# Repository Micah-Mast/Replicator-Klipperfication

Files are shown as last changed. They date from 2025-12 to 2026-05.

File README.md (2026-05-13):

# Replicator-Klipperfication

## Abstract

The intent of this project was to revive a MakerBot Replicator+ by replacing its proprietary control system with modern, open-source electronics. The original printer, while capable in its time, had been put out of service in part due to its discontinued parts and incompatibility with modern slicers. By installing a BTT Pi, SKR Mini E3, and open-source Klipper software, the printer was brought up to current standards while retaining its original mechanical frame and gantry system. Every part of the machine, with the exception of the frame and gantry, can now be sourced from online retailers or 3d printed. Throughout the build, several unexpected issues arose, including failures in the Pi's stock 24 V buck converter and incompatibility with the first purchased touchscreen, but these were resolved with alternative hardware. The result is a fully functional, easily maintainable printer that offers improved print quality, faster workflow, and long-term serviceability using only open-source tools and components.

<p align="center">
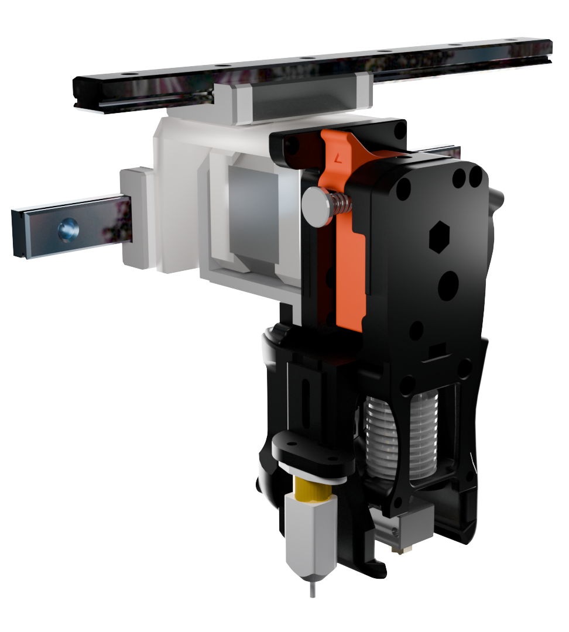
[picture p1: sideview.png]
Side view
  
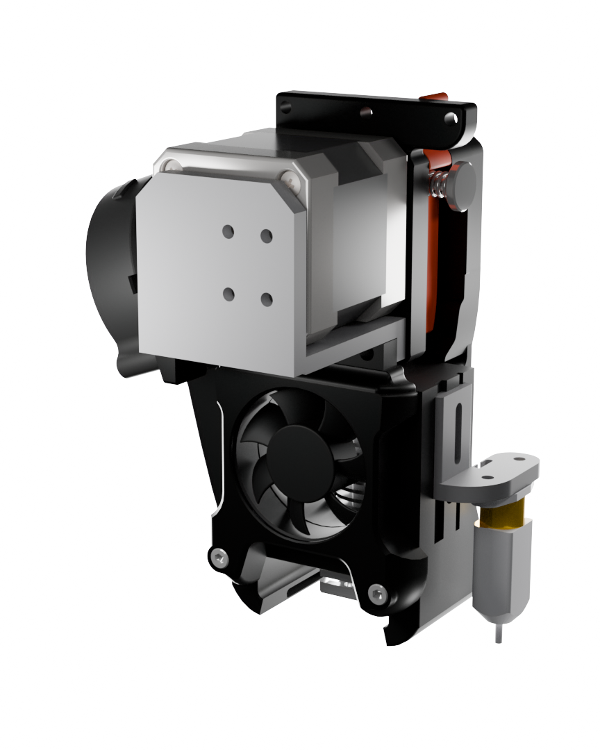
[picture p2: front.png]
Front view
  
</p>

More information can be found in the [full report](report.pdf).

## Bill Of Materials

| Component | Part | Price | Notes | Link |
|---|---|---|---|---|
| Control Board | BTT Pi V1.2 | 32 |  Stock 24v Buck converter may fail | https://a.co/d/30Qcsj7|
| Motor Controller | SKR Mini E3 V3 | 44 |  bought in combo with BTT Pi  | https://a.co/d/30Qcsj7 |
| Extruder | BMG Extruder | 6.53  | | https://www.aliexpress.us/item/3256805805447850.html |
| Heating Core | Triangle Lab CHC Pro | 5.53  | | https://www.aliexpress.us/item/3256804038017822.html |
| Heatsink + Heatbreak | V6 Heatsink | 7.58  | | https://www.aliexpress.us/item/3256802721411891.html |
| Nozzle | Came with Heatsink | | | |
| Screen | MPI3501 | 10.25 | | https://www.aliexpress.us/item/3256804172295020.html |
| Touch Panel | 3.7\" Resistive Touch Panel | 6.68  | | https://www.aliexpress.us/item/3256806894168830.html |
| BLTouch | 3DTouch | 10.87 | This is a decent BLTouch clone  | https://www.aliexpress.us/item/3256802648193836.html |
| Wires | Stepper Motor Wires | varies |  any standard stepper wires can be used | https://a.co/d/eqlczG9 |
| Power Supply | Creality 24V Power Supply | 30 | can be obtained from an Ender 3 |https://a.co/d/9iuD99J|
| Input Shaping Sensor | ADXL345 | 16 | | https://a.co/d/dzSP3lk |
| Heated Bed | Ender 3 Heated Bed | 24 | | https://a.co/d/fFlMreV |
| HDMI Adapter | Micro HDMI to HDMI Adapter | 3.49  | | https://www.aliexpress.us/item/3256803000529672.html |
| 5V Buck Converter | 24 → 5V Buck Converter | 7.49  | Overkill and only needed if onboard one fails | https://www.aliexpress.us/item/2255799834871688.html |
| Touch Screen Adapter | AR1100 Resistive Touch → USB Controller | 9.95  | | https://www.amazon.com/Noctua-NF-A4x10-24V-PWM-Applications/dp/B0CN39MCPL |

## Ideas for the Future
New Nozzle - I think the current nozzle is the main source of bad prints currently. 
Cable Management - The way the cables currently hang could very well get in the way of a print. They are also an eyesore. The wires in the back panel also need some work. Not all wires have the correct connector so they are hotglued to the controller. This has caused problems with motors vibrating loose over time.
USB hub in the UI console - Adding this would reduce the amount of wires going to the screen from 4 down to 1. The BTT-Pi can output video over USB-C so not only would the usb cables be reduced to one but the HDMI cable could be removed as well.
Input Shaping - I bought an input shaper but ran out of time to set it up fully. This would improve print quality without much effort and some of my efforts can be found in the input_shaper.cfg file.
PEI Bed - This was a result of cost, but magnetic PEI beds are not absurdly expensive for the size bed on this printer and would immediately improve the ease-of-use of the printer compared to the glass bed on there now.
Reprint Printhead in Black and Red - not a necessary upgrade but it would be nice if the actual product matched the renders.
Foodsafe Upgrade - it would be cool to turn this into a printer designated to printing food-safe filament. Really the only components that would need to be changed are the nozzle and heatbreak which need to be upgraded anyway.
Fine-Tune Slicer Settings - This is another thing that just takes time that I did not have. It just takes a lot of measuring and test prints.

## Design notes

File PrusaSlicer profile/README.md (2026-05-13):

# Using this config.ini
In PrusaSlicer under the File dropdown, choose **Import** and then **Import Config Bundle** and then navigate to the config.ini in this folder.

# Known Issue
The files for the custom bed texture and model fail to import automatically so they must be applied manually. This is not necessary for the slicer to work but it makes it look nicer.
In the **Printers** menu, click the **Set** button next to **Bed Shape** and import the files with their respective buttons.

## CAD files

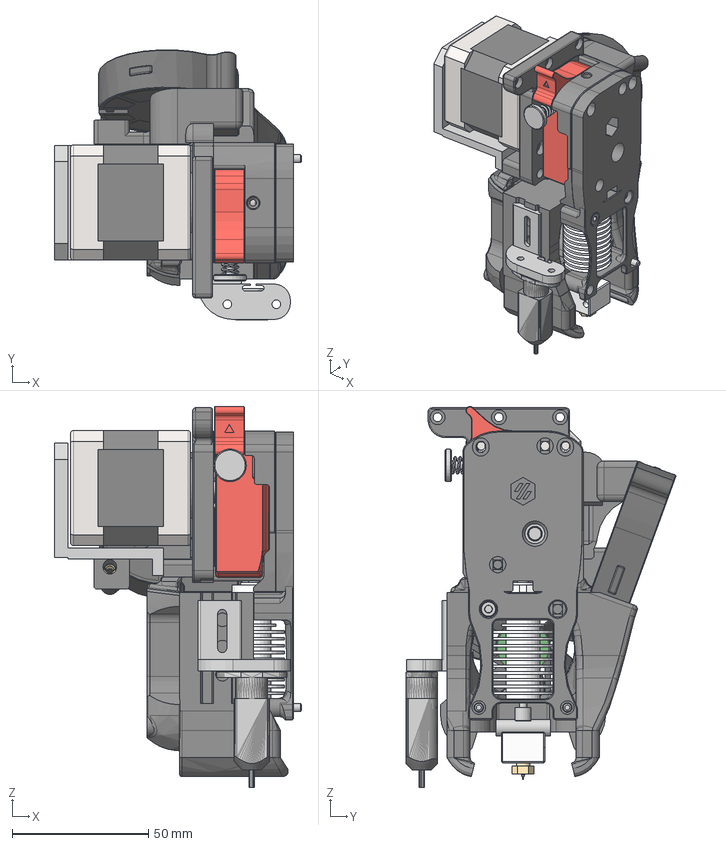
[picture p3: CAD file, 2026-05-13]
CAD/Afterburner_Assembly.step
90.8 x 99.2 x 139.9 mm
Extruder Motor Plate
shafft 3 x 20
M3x5x7 Needlebearing x 2
Direct_Drivegear_without_setscrew (1)
M3 Threaded Insert (1) x 3
M3 Thumb Screw (1)^Spring Assembly (1)_Guidler_VORON Clockwork_X Carr iage
Spring Assembly (1)-40^Spring Assembly (1)_Guidler_VORON Clockwork_X Carriage
Latch
Shaft-assembly
MR85 Ballbearing 5x8x2 x 2
Direct_Drivegear
Bowden
40x40x10 DC Fan
M3x12 SHCS (1) x 2
E3D V6 Body Rear
Heatbreak
Nozzle
Heat Block
Ceramic Cartridge Heater
Heatsink
PTFE Tube (40mm)
DragonflyBMS_Body_Front
M3x40 SHCS (3)
M3x40 SHCS (4)
M3x16 SHCS (12)
Radial_Fan_50x15
Base
Cuerpo
Tapa
pan cross head_am_B18.6.7M - M3 x 0.5 x 5 Type I Cross Recessed PHMS --5N x 4
Eje
instrument ball bearing_68_am_AFBMA 12.1.4.1 - 0050-11 - 10,SI,NC,10_ 68 x 2
socket button head cap screw_am_B18.3.4M - 3 x 0.5 x 5 SBHCS --N

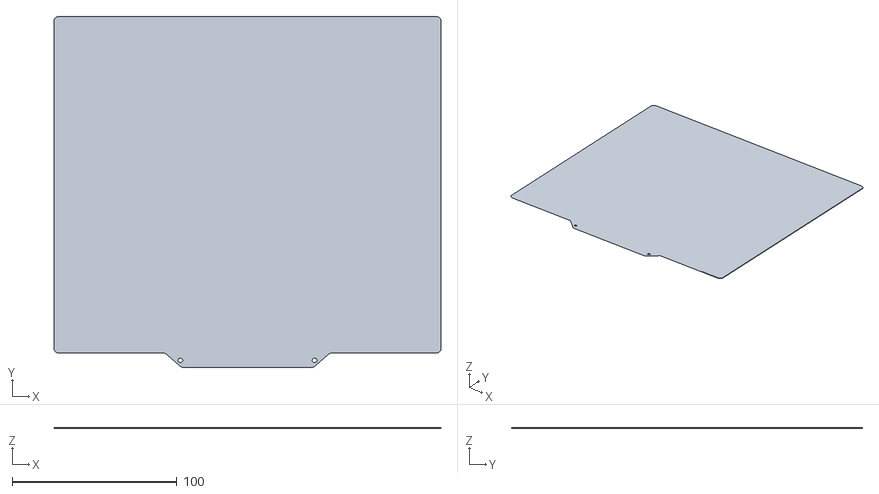
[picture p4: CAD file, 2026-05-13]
PrusaSlicer profile/replicator_bed.stl
235.0 x 213.2 x 0.5

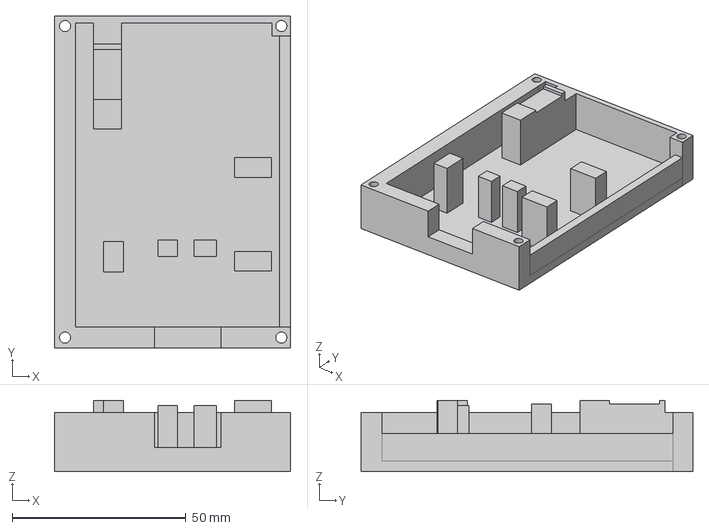
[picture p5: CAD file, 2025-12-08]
CAD/LCD_Display.step
67.9 x 95.5 x 20.5 mm

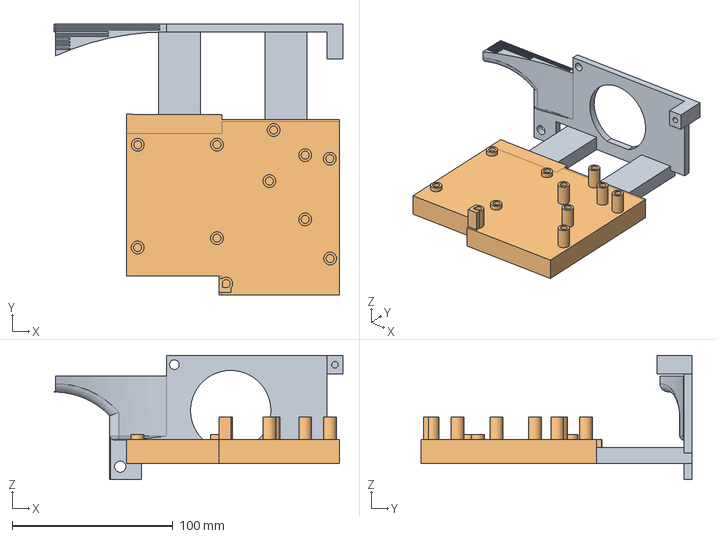
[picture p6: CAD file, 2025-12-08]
CAD/board mount.step
180.0 x 168.9 x 77.5 mm

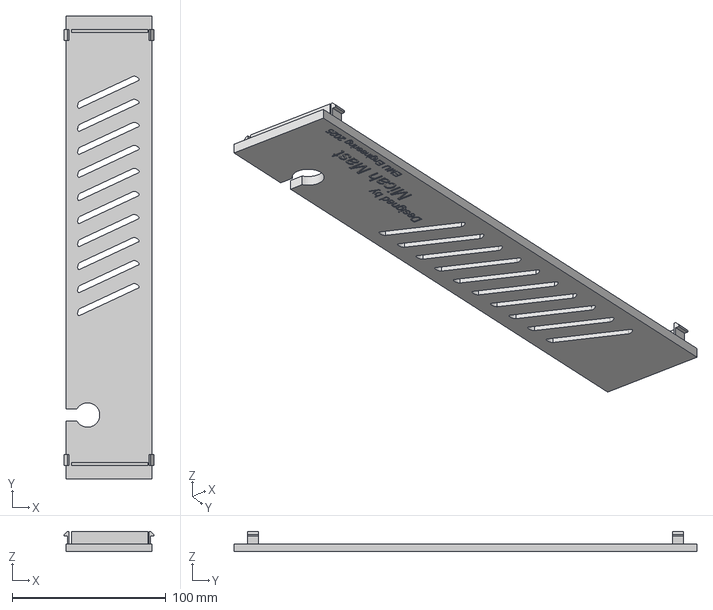
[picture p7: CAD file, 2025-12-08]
CAD/back cover.step
58.3 x 301.4 x 13.1 mm

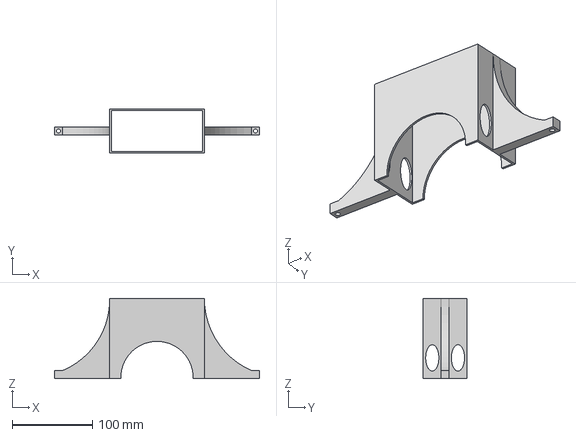
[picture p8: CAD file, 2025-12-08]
CAD/PSU mount.step
255.5 x 55.0 x 100.0 mm

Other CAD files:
CAD/LCD_Display.f3d
CAD/PSU mount.f3d
CAD/back cover.f3d

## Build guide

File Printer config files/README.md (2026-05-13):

# Using these Files
These files belong on the printer itself and can be accessed using the web GUI. The GUI can be accessed by going to replicator.local on the same network as the printer. The MAC Address can be found on a sticker on the bottom of the BTT-Pi.

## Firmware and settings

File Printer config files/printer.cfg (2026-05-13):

[include mainsail.cfg]
[include gcode_macros.cfg]
#[include input_shaper.cfg] uncomment only when calibrating input shaper and accelerometer is plugged in
#[input_shaper]
#shaper_type_x = 2hump_ei
#haper_freq_x = 68.4
#shaper_type_y = ei
#haper_freq_y = 83.8
# host MCU service is preinstalled and ready to use with:
[mcu CB1]
serial: /tmp/klipper_host_mcu

# This file contains common pin mappings for the BIGTREETECH SKR mini
# E3 v3.0. To use this config, the firmware should be compiled for the
# STM32G0B1 with a "8KiB bootloader" and USB communication/USART.

# The "make flash" command does not work on the SKR mini E3. Instead,
# after running "make", copy the generated "out/klipper.bin" file to a
# file named "firmware.bin" on an SD card and then restart the SKR
# mini E3 with that SD card.

# See docs/Config_Reference.md for a description of parameters.
[gcode_arcs]
resolution: 1.0
#   An arc will be split into segments. Each segment's length will
#   equal the resolution in mm set above. Lower values will produce a
#   finer arc, but also more work for your machine. Arcs smaller than
#   the configured value will become straight lines. The default is
#   1mm.

[bltouch]
sensor_pin: ^PC14 #Remove ^ if print head crashes into bed, the ^ is for the CR touch a bl touch should work without.
control_pin: PA1
x_offset: 39
y_offset: -2
z_offset: 0.40
#speed:

#[safe_z_home]
#home_xy_position: 115,115 # Change coordinates to the center of your print bed
#speed: 50
#z_hop: 10                 # Move up 10mm
#z_hop_speed: 5

[bed_mesh]
speed: 120
horizontal_move_z: 5
mesh_min: 0, 2
mesh_max: 225, 190
probe_count: 5,5
adaptive_margin: 5

[stepper_x]
step_pin: PB13
dir_pin: !PB12
enable_pin: !PB14
microsteps: 16
rotation_distance: 36
homing_positive_dir: false
endstop_pin: tmc2209_stepper_x:virtual_endstop
position_min: -49
position_endstop: -49
homing_retract_dist: 0
position_max: 254
homing_speed: 50

[tmc2209 stepper_x]
uart_pin: PC11
tx_pin: PC10
uart_address: 0
run_current: 0.80
#stealthchop_threshold: 999999
diag_pin: ^PC0
driver_SGTHRS: 117

[stepper_y]
step_pin: PB10
dir_pin: PB2
enable_pin: !PB11
microsteps: 16
rotation_distance: 36
homing_positive_dir: false
endstop_pin: tmc2209_stepper_y:virtual_endstop
position_min: 0
position_endstop: 0
homing_retract_dist: 0
position_max: 199
homing_speed: 50

[tmc2209 stepper_y]
uart_pin: PC11
tx_pin: PC10
uart_address: 2
run_current: 0.80
stealthchop_threshold: 999999
diag_pin: ^PC1
driver_SGTHRS: 107

[stepper_z]
step_pin: PB0
dir_pin: !PC5
enable_pin: !PB1
microsteps: 16
rotation_distance: 8
# endstop_pin: ^PC2
# position_endstop: 0.0
endstop_pin: probe:z_virtual_endstop
position_max: 125
position_min: -2

[tmc2209 stepper_z]
uart_pin: PC11
tx_pin: PC10
uart_address: 1
run_current: 0.580
hold_current: 0.500
stealthchop_threshold: 999999

[extruder]
step_pin: PB3
dir_pin: !PB4
enable_pin: !PD1
microsteps: 16
rotation_distance: 7.71052
nozzle_diameter: 0.400
filament_diameter: 1.750
heater_pin: PC8
sensor_type: EPCOS 100K B57560G104F
sensor_pin: PA0
#control: pid
#pid_Kp: 21.527
#pid_Ki: 1.063
#pid_Kd: 108.982
min_temp: 0
max_temp: 300

[tmc2209 extruder]
uart_pin: PC11
tx_pin: PC10
uart_address: 3
run_current: 0.80
#hold_current: 0.500
stealthchop_threshold: 999999

[heater_bed]
heater_pin: PC9
sensor_type: ATC Semitec 104GT-2
sensor_pin: PC4
control: pid
pid_Kp: 54.027
pid_Ki: 0.770
pid_Kd: 948.182
min_temp: 0
max_temp: 130

#[heater_fan controller_fan]
#pin: PB15
#heater: heater_bed
#heater_temp: 45.0

[heater_fan nozzle_cooling_fan]
pin: PC7

[fan]
pin: PC6

[mcu]
serial: /dev/serial/by-id/usb-Klipper_stm32g0b1xx_4A00380012504D5930363820-if00
# serial: /dev/ttyAMA0
# restart_method: command

[printer]
kinematics: corexy
max_velocity: 300
max_accel: 3000
max_z_velocity: 25
max_z_accel: 30

[board_pins]
aliases:
    # EXP1 header
    EXP1_1=PB5,  EXP1_3=PA9,   EXP1_5=PA10, EXP1_7=PB8, EXP1_9=<GND>,
    EXP1_2=PA15, EXP1_4=<RST>, EXP1_6=PB9,  EXP1_8=PD6, EXP1_10=<5V>


######################################################################
#  BigTreeTech TFT TouchScreen emulated 12864 mode
######################################################################

[display]
lcd_type: emulated_st7920
spi_software_miso_pin: PD8 # status led, Virtual MISO
spi_software_mosi_pin: PD6
spi_software_sclk_pin: PB9
en_pin: PB8
encoder_pins: ^PA10, ^PA9
click_pin: ^!PA15

[output_pin beeper]
pin: PB5

#*# <---------------------- SAVE_CONFIG ---------------------->
#*# DO NOT EDIT THIS BLOCK OR BELOW. The contents are auto-generated.
#*#
#*# [extruder]
#*# control = pid
#*# pid_kp = 18.033
#*# pid_ki = 1.179
#*# pid_kd = 68.977
#*#
#*# [bltouch]
#*#
#*# [bed_mesh default]
#*# version = 1
#*# points =
#*# 	0.400000, 0.435000, 0.260000, 0.187500, 0.080000
#*# 	0.222500, 0.207500, 0.152500, 0.102500, 0.077500
#*# 	0.047500, 0.025000, 0.107500, 0.027500, -0.047500
#*# 	-0.072500, -0.117500, -0.060000, -0.075000, -0.045000
#*# 	-0.182500, -0.187500, -0.162500, -0.147500, -0.110000
#*# x_count = 5
#*# y_count = 5
#*# mesh_x_pps = 2
#*# mesh_y_pps = 2
#*# algo = lagrange
#*# tension = 0.2
#*# min_x = 0.0
#*# max_x = 225.0
#*# min_y = 2.0
#*# max_y = 190.0

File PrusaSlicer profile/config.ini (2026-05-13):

[vendor]
name = MakerBot
config_version = 1.0.0

[printer_model:Replicator+]
name = Replicator+
bed_model = replicator_bed.stl
bed_texture = replicator_bed.svg
default_materials = Replicator+ Default 0.4

# All presets starting with asterisk, for example *common*, are intermediate and they will
# not make it into the user interface.

# Common print presets

[print:Replicator+]
arc_fitting = emit_center
automatic_extrusion_widths = 0
automatic_infill_combination = 0
automatic_infill_combination_max_layer_height = 100%
avoid_crossing_curled_overhangs = 0
avoid_crossing_perimeters = 0
avoid_crossing_perimeters_max_detour = 0
bed_temperature_extruder = 0
bottom_fill_pattern = monotonic
bottom_solid_layers = 3
bottom_solid_min_thickness = 0.5
bridge_acceleration = 500
bridge_angle = 0
bridge_flow_ratio = 1
bridge_speed = 40
brim_separation = 0
brim_type = outer_only
brim_width = 0
compatible_printers = 
compatible_printers_condition = 
complete_objects = 0
custom_parameters_print = 
default_acceleration = 2500
dont_support_bridges = 0
draft_shield = disabled
elefant_foot_compensation = 0.2
enable_dynamic_overhang_speeds = 1
ensure_vertical_shell_thickness = enabled
external_perimeter_acceleration = 2500
external_perimeter_extrusion_width = 0.45
external_perimeter_speed = 150
external_perimeters_first = 0
extra_perimeters = 0
extra_perimeters_on_overhangs = 0
extrusion_width = 0.45
fill_angle = 45
fill_density = 15%
fill_pattern = grid
first_layer_acceleration = 0
first_layer_acceleration_over_raft = 0
first_layer_extrusion_width = 0.5
first_layer_height = 0.2
first_layer_infill_speed = 0
first_layer_speed = 40
first_layer_speed_over_raft = 30
fuzzy_skin = none
fuzzy_skin_point_dist = 0.8
fuzzy_skin_thickness = 0.3
gap_fill_enabled = 1
gap_fill_speed = 80
gcode_comments = 0
gcode_label_objects = disabled
gcode_resolution = 0.008
gcode_substitutions = 
infill_acceleration = 1500
infill_anchor = 2
infill_anchor_max = 12
infill_every_layers = 1
infill_extruder = 1
infill_extrusion_width = 0.45
infill_first = 0
infill_overlap = 15%
infill_speed = 180
inherits = 
interface_shells = 0
interlocking_beam = 0
interlocking_beam_layer_count = 2
interlocking_beam_width = 0.8
interlocking_boundary_avoidance = 2
interlocking_depth = 2
interlocking_orientation = 22.5
ironing = 0
ironing_flowrate = 15%
ironing_spacing = 0.1
ironing_speed = 15
ironing_type = top
layer_height = 0.2
max_print_speed = 180
max_volumetric_extrusion_rate_slope_negative = 0
max_volumetric_extrusion_rate_slope_positive = 0
max_volumetric_speed = 0
min_bead_width = 85%
min_feature_size = 25%
min_skirt_length = 0
mmu_segmented_region_interlocking_depth = 0
mmu_segmented_region_max_width = 0
notes = 
only_one_perimeter_first_layer = 0
only_retract_when_crossing_perimeters = 0
ooze_prevention = 0
output_filename_format = [input_filename_base].gcode
over_bridge_speed = 0
overhang_speed_0 = 15
overhang_speed_1 = 25
overhang_speed_2 = 30
overhang_speed_3 = 80%
overhangs = 1
perimeter_acceleration = 3000
perimeter_extruder = 1
perimeter_extrusion_width = 0.45
perimeter_generator = arachne
perimeter_speed = 150
perimeters = 2
post_process = 
print_settings_id = 
raft_contact_distance = 0.1
raft_expansion = 1.5
raft_first_layer_density = 80%
raft_first_layer_expansion = 3.5
raft_layers = 0
resolution = 0
scarf_seam_entire_loop = 0
scarf_seam_length = 20
scarf_seam_max_segment_length = 1
scarf_seam_on_inner_perimeters = 0
scarf_seam_only_on_smooth = 1
scarf_seam_placement = nowhere
scarf_seam_start_height = 0%
seam_gap_distance = 15%
seam_position = aligned
single_extruder_multi_material_priming = 1
skirt_distance = 6
skirt_height = 1
skirts = 1
slice_closing_radius = 0.049
slicing_mode = regular
small_perimeter_speed = 150
solid_infill_acceleration = 4000
solid_infill_below_area = 0
solid_infill_every_layers = 0
solid_infill_extruder = 1
solid_infill_extrusion_width = 0.45
solid_infill_speed = 180
spiral_vase = 0
staggered_inner_seams = 0
standby_temperature_delta = -5
support_material = 0
support_material_angle = 0
support_material_auto = 1
support_material_bottom_contact_distance = 0
support_material_bottom_interface_layers = 0
support_material_buildplate_only = 0
support_material_closing_radius = 2
support_material_contact_distance = 0.2
support_material_enforce_layers = 0
support_material_extruder = 1
support_material_extrusion_width = 0.35
support_material_interface_contact_loops = 0
support_material_interface_extruder = 1
support_material_interface_layers = 5
support_material_interface_pattern = auto
support_material_interface_spacing = 0.2
support_material_interface_speed = 100%
support_material_pattern = rectilinear
support_material_spacing = 2
support_material_speed = 100
support_material_style = organic
support_material_synchronize_layers = 0
support_material_threshold = 40
support_material_with_sheath = 1
support_material_xy_spacing = 80%
support_tree_angle = 40
support_tree_angle_slow = 25
support_tree_branch_diameter = 2
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

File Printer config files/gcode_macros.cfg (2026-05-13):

#########################################################
#                       MACROS                          #
#-------------------------------------------------------#
# This file contains all the G-code macros used by this #
# printer, including:                                    #
#   - Homing                                             #
#   - Pausing / Resuming                                 #
#   - Starting Prints                                    #
#   - Loading / Unloading Filament                      #
#########################################################

[homing_override]
set_position_z: 0
axes: xyz
gcode:
    {% set home_x = ('X' in params|default({})) %}
    {% set home_y = ('Y' in params|default({})) %}
    {% set home_z = ('Z' in params|default({})) %}
    {% set home_all = (not (home_x or home_y or home_z)) %}

    {% if home_all %}
        SENSORLESS_HOME_X
        SENSORLESS_HOME_Y
        BLTOUCH_HOME_Z
    {% else %}
        {% if home_x %}
            SENSORLESS_HOME_X
        {% endif %}
        {% if home_y %}
            SENSORLESS_HOME_Y
        {% endif %}
        {% if home_z %}
            BLTOUCH_HOME_Z
        {% endif %}
    {% endif %}
    
[gcode_macro SENSORLESS_HOME_X]
gcode:
    {% set HOME_CUR = 0.700 %}
    {% set driver_config = printer.configfile.settings['tmc2209 stepper_x'] %}
    {% set RUN_CUR = driver_config.run_current %}
    # Set current for sensorless homing
    SET_TMC_CURRENT STEPPER=stepper_x CURRENT={HOME_CUR}
    # Pause to ensure driver stall flag is clear
    G4 P2000
    # Home
    G28 X0
    G90
    G1 X115 F1500

    # Set current during print
    SET_TMC_CURRENT STEPPER=stepper_x CURRENT={RUN_CUR}

[gcode_macro SENSORLESS_HOME_Y]
gcode:
    {% set HOME_CUR = 0.700 %}
    {% set driver_config = printer.configfile.settings['tmc2209 stepper_y'] %}
    {% set RUN_CUR = driver_config.run_current %}
    # Set current for sensorless homing
    SET_TMC_CURRENT STEPPER=stepper_y CURRENT={HOME_CUR}
    # Pause to ensure driver stall flag is clear
    G4 P2000
    # Home
    G28 Y0
    # Move away
    G90
    G1 Y115 F1500
    # Set current during print
    SET_TMC_CURRENT STEPPER=stepper_y CURRENT={RUN_CUR}

[gcode_macro BLTOUCH_HOME_Z]
gcode:
    G28 Z0
    G90
    G1 Z25 F1500
  

[gcode_macro START_PRINT]
description: Start print with homing, heating, and nozzle purge line
gcode:
    {% set BED_TEMP = params.BED|default(60)|float %}
    {% set EXTRUDER_TEMP = params.EXTRUDER|default(200)|float %}

    # Set temps
    M140 S{BED_TEMP}  ; start heating bed
    M104 S{EXTRUDER_TEMP}             ; start heating nozzle
    

    # Home all axes
    G28

    # Create bed mesh for just the model area (doesn't work currently)
    #BED_MESH_CLEAR
    #BED_MESH_CALIBRATE
    # Move up to prevent scratching
    G1 Z5 F6000
    M109 S{EXTRUDER_TEMP}             ; wait for nozzle

    # Move off the front right edge of the bed
    G1 X-25 Y0 F6000 

    G1 E10 F300               ; slow pre-extrusion

    # Prime line
    G92 E0
    G1 Z1 F1000
    G1 X30 E10 Z0.3 F1000
   

    G92 E0

    # Ready to print
    G90
    M117 Printing...

[gcode_macro _TOOLHEAD_PARK_PAUSE_CANCEL]
description: Helper: park toolhead used in PAUSE and CANCEL_PRINT
variable_extrude: 1.0
gcode:
  ##### set park position for x and y #####
  # default is max position from printer.cfg
  # doesn't work on end print I don't think
  {% set x_park = -49 %}
  {% set y_park = 199 %}
  {% set z_park_delta = 2.0 %}
  ##### calculate save lift position #####
  {% set max_z = printer.toolhead.axis_maximum.z|float %}
  {% set act_z = printer.toolhead.position.z|float %}
  {% if act_z < (max_z - z_park_delta) %}
    {% set z_safe = z_park_delta %}
  {% else %}
    {% set z_safe = max_z - act_z %}
  {% endif %}
  ##### end of definitions #####
  {% if printer.extruder.can_extrude|lower == 'true' %}
    M83
    G1 E-{extrude} F2100
    {% if printer.gcode_move.absolute_extrude |lower == 'true' %} M82 {% endif %}
  {% else %}
    {action_respond_info("Extruder not hot enough")}
  {% endif %}
  {% if "xyz" in printer.toolhead.homed_axes %}
    G91
    G1 Z{z_safe} F900
    G90
    G1 X{x_park} Y{y_park} F6000
    {% if printer.gcode_move.absolute_coordinates|lower == 'false' %} G91 {% endif %}
  {% else %}
    {action_respond_info("Printer not homed")}
  {% endif %}

[gcode_macro LOAD_FILAMENT]
variable_load_distance: 40         # Distance to load filament into the extruder
variable_purge_distance: 100        # Distance to purge filament after loading
variable_nozzle_preheat_temp: 210  # Default preheat temperature for the nozzle
variable_turn_off_extruder: True   # Option to turn off the extruder after loading (True/False)
gcode:
    # Parameters and settings
    {% set load_speed = params.LOAD_SPEED|default(600) %}  # Speed in mm/min for fast filament loading
    {% set purge_speed = params.PURGE_SPEED|default(300) %}  # Speed in mm/min for purging filament
    {% set target_temp = params.TARGET_TEMP|default(nozzle_preheat_temp) %}  # Target temperature for the nozzle
    {% set min_temp = params.MIN_TEMP|default(180) %}  # Minimum safe temperature for extrusion

    # Save current state of the printer
    SAVE_GCODE_STATE NAME=load_state

    # Heat directly to the target temperature if it's above the minimum temperature
    {% if target_temp >= min_temp %}
        M104 S{target_temp} ; Set extruder to target temperature
        M109 S{target_temp} ; Wait for extruder to reach target temperature
    {% else %}
        # Heat to minimum temperature first if target is too low
        M104 S{min_temp} ; Set extruder to safe minimum temperature
        M109 S{min_temp} ; Wait for extruder to reach safe minimum temperature
    {% endif %}

    # Begin filament loading process
    G91 ; Set relative positioning for extrusion
    G92 E0 ; Reset extruder position
    G1 E{load_distance} F{load_speed} ; Load filament at the specified loading speed
    G1 E{purge_distance} F{purge_speed} ; Purge filament at the slower purging speed

    # Optionally turn off the extruder heater after loading
    {% if turn_off_extruder %}
        M400
        M104 S0 ; Turn off extruder heater
    {% endif %}

    # Restore previous state of the printer
    G90 ; Restore absolute positioning
    RESTORE_GCODE_STATE NAME=load_state

    # Completion message
    M117 Filament load complete

[gcode_macro UNLOAD_FILAMENT]
variable_unload_distance: 50      # Distance to retract filament from the extruder
variable_nozzle_preheat_temp: 210  # Default preheat temperature for unloading
variable_turn_off_extruder: True   # Option to turn off the extruder after unloading (True/False)
gcode:
    # Parameters and settings
    {% set retract_speed = params.RETRACT_SPEED|default(600) %}  # Speed for retracting filament
    {% set target_temp = params.TARGET_TEMP|default(nozzle_preheat_temp) %}  # Target temperature for the nozzle
    {% set min_temp = params.MIN_TEMP|default(180) %}  # Minimum safe temperature for extrusion

    # Save current state of the printer
    SAVE_GCODE_STATE NAME=unload_state

    # Heat the nozzle to the target temperature if required
    {% if printer.extruder.temperature < target_temp %}
        # Ensure the nozzle is heated to the target temperature or at least the minimum safe temperature
        {% if target_temp >= min_temp %}
            M104 S{target_temp} ; Set extruder to target temperature
            M109 S{target_temp} ; Wait for extruder to reach target temperature
        {% else %}
            M104 S{min_temp} ; Set extruder to safe minimum temperature
            M109 S{min_temp} ; Wait for extruder to reach safe minimum temperature
        {% endif %}
    {% endif %}

    # Begin filament unloading process
    G91 ; Set relative positioning for extrusion
    G92 E0 ; Reset extruder position
    G1 E-{unload_distance} F{retract_speed} ; Retract filament at the specified speed
    G1 E-{unload_distance} F{retract_speed} ; Repeat since 100 is above the max

    # Optionally turn off the extruder heater after unloading
    {% if turn_off_extruder %}
        M400
        M104 S0 ; Turn off extruder heater
    {% endif %}

    # Restore previous state of the printer
    G90 ; Restore absolute positioning
    RESTORE_GCODE_STATE NAME=unload_state

    # Completion message
    M117 Filament unload complete

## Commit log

2025-12-08 Added Cad files
    [LCD_Display.f3d, LCD_Display.step, PSU mount.f3d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]
2025-12-08 update readme and add config file
    [printer.cfg]
2026-05-13 updated CAD, PrusaSlicer config, folder structure, and all printer config files
    [Afterburner_Assembly.step, gcode_macros.cfg, input_shaper.cfg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]
